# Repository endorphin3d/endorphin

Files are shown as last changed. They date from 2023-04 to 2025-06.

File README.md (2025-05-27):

# Endorphin

This is the repo for both the CAD files and the docs for the Endorphin project. Docs are built and published [here](https://endorphin3d.com/docs).

### Docs

The docs are built using [Jekyll](https://jekyllrb.com/) and [Just the Docs](https://justtheocs.com/).

To serve the docs locally, run:

```sh
bundle exec jekyll serve
```

This will start a local server at `http://localhost:4000`.

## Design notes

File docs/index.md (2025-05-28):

---
layout: default
title: Introduction
nav_order: 1
permalink: docs
has_toc: false
---

{% capture preface %}
In the last few years 3D printers have become blisteringly fast, pushing the limits of both heating and cooling while leaving those of us with printers like the Ender 5 feeling a bit left out of the fun. That ends now. Your Ender 5 is capable of being every bit as fast as a Voron without the hefty price tag. There have been [other](https://zerog.one) CoreXY [projects](https://www.printables.com/model/169131-ender-5-core-xy-with-linear-rails-mk3) to do a full conversion on the Ender 5, but often the price of parts or the complexity of the build makes it hard to justify over just buying something pre-built like a Bambulab P1P.

**The Endorphin is different.**

With a first-stage build you can do in an afternoon with parts that total less than $25, you no longer have any excuses *not* to turn Ender 5 into a speed demon.
{% endcapture %}
{% include docs-preface.html
  title="# Introduction"
  image="/assets/images/docs/getting-started/belt-path.png"
  content=preface
%}

{% capture kinematic %}
The Endorphin uses a slightly different belt setup from the original Ender 5, known as a "Markforged kinematic" or Hybrid CoreXY. In this setup the X belt moves like a CoreXY but the Y axis remains in its original Ender 5 cartesian setup.

### Why Though?

The basic idea is this: The less weight being thrown around, the faster the printer's acceleration/deceleration can be. Less weight also means higher top speeds because there will be less energy required to stop and change direction at the end of each move. This is why the CoreXY setup has become the choice of pretty much all high-speed printers such as the BambuLab, Voron, Ratrig, and HevORT.

This project moves the X stepper motor off the gantry and onto the frame, where the Y steppers won't have to lug it around anymore. This is a significant amount of weight we're saving!

Now, if you know anything about CoreXY machines you know that unlike cartesian printers, CoreXY printers don't have an "X stepper" or a "Y stepper" because a movement of one stepper affects both belts. In the Markforged kinematic, this is only partially the case:

- The X stepper can move the printhead along the X axis by simply moving its belt while the Y belt stays stationary
- The Y stepper only has to worry about moving the gantry linearly along the Y axis (cartesian style)
- BUT when the Y stepper moves the gantry, the length of the X belt on either side of the gantry is affected and thus the X stepper must also move to compensate

### Firmware

Luckily this kinematic is supported by both Klipper and the stock Marlin firmware (with a small modification). After you've printed the parts for at least stage 1, just follow the instructions in the [firmware section](/docs/firmware) to use the new kinematic.
{% endcapture %}
{% include docs-step.html
  heading="## Kinematic"
  image="/assets/images/docs/getting-started/kinematic.png"
  content=kinematic
%}

## Q&A

### What about the Ender 5 Plus?

Yes, as of version 1.1 the 5+ is also fully supported. Just make sure you don't leave slack in the X belt because that's a *long* belt path.

---

[Next →](/docs/stages){: .btn .btn-outline .fs-5 }

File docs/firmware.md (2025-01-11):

---
layout: default
title: Firmware
nav_order: 3
permalink: docs/firmware
has_toc: false
---

# Firmware

{: .warning }
Don't make these changes until *AFTER* you've printed out all the parts for at least stage 1! You need a working printer (or a second printer) to get stage 1 off the ground.

- TOC
{:toc}

---

### Klipper

If you've been thinking about making the leap to Klipper, this might be the push you've been needing. Making config changes to a machine running Klipper is roughly 1000% easier than Marlin. All that's required to configure Klipper to use the new kinematic is editing `printer.cfg` and changing `kinematics` under the `[printer]` section:

```yml
[printer]
kinematics: hybrid_corexy
...
```

Then change your endstop settings under `stepper_x` and `stepper_y` so the printer homes in the right direction:

```yml
[stepper_x]
...
position_endstop: 220
position_max: 220
...

[stepper_y]
...
# Note: These may need to be 190 if using the EVA printhead
position_endstop: 200
position_max: 200
...
```

Now save and restart and you're done. Seriously, you're done.

### Marlin (Original Firmware)

The Marlin firmware is a bit trickier. To change the kinematics here you need to recompile and flash the firmware on your board.

Start by following the instructions on the [Marlin site](https://marlinfw.org/docs/basics/install_platformio_vscode.html) until you reach the section on example configurations where you're told to "find the configuration files for your printer." Assuming you've downloaded the Marlin configurations, you'll now need to pick the folder that corresponds to your printer + board version. The surest way to figure which board you have is to open up the case and check. If you have a 4.2.7 or a 4.2.2, it'll be printed right under the Creality logo in the center of the board. If you have a v1 board, there will be no version printed at all.

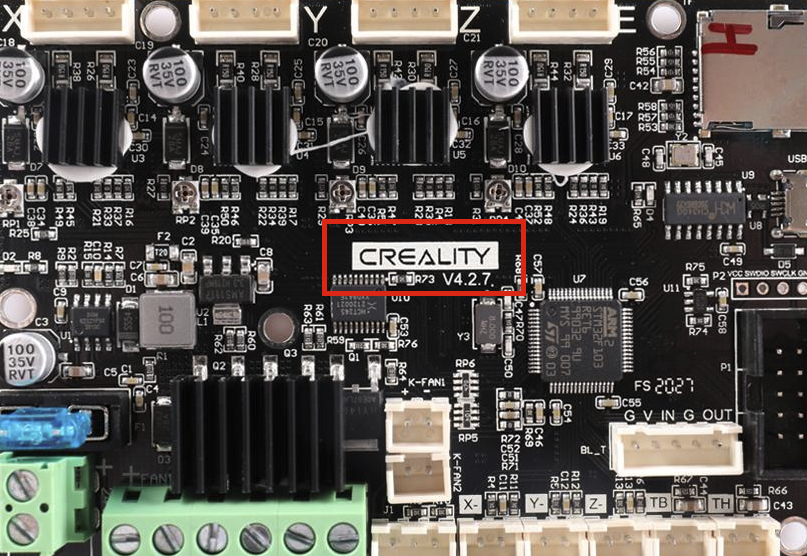
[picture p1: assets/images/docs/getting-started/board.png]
Endorphin stage 1


So for example if you have an Ender 5 Pro with a 4.2.7 board, you'll find the correct configuration in the folder `config/examples/Creality/Ender-5 Pro/CrealityV427`.

Next we need to configure the firmware to use the Markforged kinematic. This only requires editing a single line in the `Configuration.h` file. If you search the file for "MARKFORGED_XY" you should see this line several hundred lines down:

```c
//#define MARKFORGED_XY
```

You'll want to un-comment this line, like so:

```c
#define MARKFORGED_XY
```

Then just below it you'll see:

```c
#if ANY(MARKFORGED_XY, MARKFORGED_YX)
  //#define MARKFORGED_INVERSE  // Enable for an inverted Markforged kinematics belt path
#endif
```

Uncomment that middle line, so it looks like this:

```c
#if ANY(MARKFORGED_XY, MARKFORGED_YX)
  #define MARKFORGED_INVERSE  // Enable for an inverted Markforged kinematics belt path
#endif
```

Now you can continue following the Marlin guide on compiling the new firmware. Once you've compiled, you can put the new firmware file (usually `firmware.bin`) at the root of your microSD card. Just to be 100% certain the printer will recognize the new firmware, rename the file to `firmware-endorphin.bin`. Then with your printer powered off, insert the SD card and power the printer on. Wait a few minutes to ensure the install finishes, then power the printer down and remove the card. Delete `firmware-endorphin.bin` and you're done!

---

[← Back](/docs/stages/stage-3){: .btn .btn-outline .mr-4 .fs-5 }

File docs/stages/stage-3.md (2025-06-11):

---
layout: default
title: Stage 3
nav_order: 3
parent: Stages
permalink: docs/stages/stage-3
---

{% capture preface %}
> The purpose of this stage is to add a linear rail on the X axis. We'll basically be trading the weight from the original steel printhead carriage and its wheels for an MGN9 rail of similar weight (on the plus side, in the Hybrid CoreXY configuration the weight will now be shared between the two stepper motors). Thus, the benefits of this stage aren't as much weight removal as the ability to use a modern printhead such as the Ratrig EVA or the Vz Printhead, plus complete liberation from those frustrating v-slot wheels.
{: .fs-5 .fw-300 .text-grey-dk-100 .text-justify }
{% endcapture %}
{% include docs-preface.html
  title="# Stage 3: Linear X Rail"
  image="/assets/images/docs/stages/stage-3/stage-3-render-lg.png"
  content=preface
%}

---

## Bill Of Materials

#### Linear Rails

| Size | Length | Quantity | Link |
| :--- | :----- | :--- | :--- |
| MGN9H Rail+Block | 350mm  | 1 | [Amazon](https://www.amazon.com/gp/product/B09XQ53J42), [Fabreeko](https://www.fabreeko.com/collections/honeybadger/products/honeybadger-mgn9h-black-steel-rails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) |

#### Bolts

| Part | Type | Quantity | Link |
| :--- | :--- | :--- | :--- |
| M3x8 socket head | ISO 4762, DIN 912 | 8 | [Amazon](https://www.amazon.com/gp/product/B08R3GJGWT) |

#### T-Nuts

| Size | Quantity | Link |
| :--- | :--- | :--- |
| M3 2020 T-nuts | 8 | [Amazon](https://www.amazon.com/gp/product/B08NZMD2BJ) |

---

## Printing

**STL files for this stage are** [here](https://github.com/endorphin3d/endorphin/tree/main/STLs/stage-3)

{% capture vz %}
**Usable Print Area:** 220 x 200 (20mm reduction on Y axis)

The Vz Printhead is an impressively simple printhead used on the blazing fast VzBot printer. It has all the features you'd expect from a modern printhead including many popular hotends, extruders, and Z probes (BLTouch and SuperPINDA). It also as well as some less-common features like adjustable-height fan ducts and CPAP cooling.

The only drawback with this printhead is that you may not already have the [30mm standoffs](https://speedyfpv.com/products/10pcs-m3x30mm-aluminum-spacer-standoff-silver-anodized?variant=37983057936557) on hand to complete the build (< $10 with shipping).

The official design only required three parts to be modified in order to work on the Endorphin. So start by downloading the official STLs from [here](https://github.com/VzBoT3D/Vz-Printhead-Printed/tree/main/STLs) and you can find the BOM [here](https://github.com/VzBoT3D/Vz-Printhead-Printed/tree/main/BOM). Then before you start printing parts, check the table below and substitute any of the original parts listed below with the Endorphin part:

| Original Part | Endorphin Part |
| :--- | :--- |
| Back plate round standoff.stl | [vz-back_plate.stl](https://raw.githubusercontent.com/endorphin3d/endorphin/main/STLs/stage-3/vz-back_plate.stl) |
| Bottom plate round standoff.stl | [vz-bottom_plate.stl](https://raw.githubusercontent.com/endorphin3d/endorphin/main/STLs/stage-3/vz-bottom_plate.stl) |
| Front round standoff.stl | [vz-front.stl](https://raw.githubusercontent.com/endorphin3d/endorphin/main/STLs/stage-3/vz-front.stl) |

{: .note }
Make sure you print the MGN9**H** version of the carriage top (assuming you bought your rails from the links above) rather than the MGN9**C** version.
{% endcapture %}
{% include docs-step.html
  heading="## Vz Printhead"
  image="/assets/images/docs/stages/stage-3/vz.png"
  content=vz
%}

### Belt Clips

Either of the following belt clips provided with the printhead will work fine so pick whichever one you prefer. The original Vz printhead has been modified so that the posts sit at the right height for the Endorphin belts. Just remember that you only need to print off clips for 2 belt ends rather than the 4 needed in a CoreXY, which means you can choose whether you want to attach the belt ends on the front or rear posts (just don't do one front and one rear). The other side will be unused.
{: .mb-8 }

{% capture belts1 %}
This clip is incredibly simple to print and the gripping mechanism is equally simple: By circling the belt around the standoffs, teeth inward, the belt grips itself by interlacing its own teeth like a zipper. This is probably the best choice in terms of printability and simplicity.
{% endcapture %}
{% include docs-step.html
  heading="#### Belt Clip Style 1"
  image="/assets/images/docs/stages/stage-3/belt-clip-1.png"
  content=belts1
%}

{% capture belts2 %}
This is a two-part clip that has more intricate details to print, so make sure to use a small enough nozzle and/or thin layers. While also a clever design, it does look like the wings on the outer clip housing run the risk of spreading under enough tension and allowing the belt to slip.
{% endcapture %}
{% include docs-step.html
  heading="#### Belt Clip Style 2"
  image="/assets/images/docs/stages/stage-3/belt-clip-2.png"
  content=belts2
%}

{% capture eva %}
**Usable Print Area:** 220 x 190 (30mm reduction on Y axis)

The EVA printhead is the standard Ratrig printhead. It has a large number of official addons including fan ducts, hotends, and extruders as well as [even more](https://www.printables.com/search/models?q=tag:eva3) parts created by the community. The main downside of this printhead is that its size causes about 10mm more lost print space on the Y axis than the Vz.

The official EVA v3 design only required three parts to be modified in order to work on the Endorphin, so you can start by reading up on the official [CoreXY printhead](https://main.eva-3d.page/heat_insert/core/corexy) and downloading most of the parts from this page. Just substitute the following parts for the Endorphin versions in this table:

| Original Part | Endorphin Part |
| :--- | :--- |
| back_core_xy_fi.stl | [eva-back_endorphin.stl](https://raw.githubusercontent.com/endorphin3d/endorphin/main/STLs/stage-3/eva-back_endorphin.stl) |
| core_xy_belt_grabber.stl | [eva-endorphin_belt_grabber.stl](https://raw.githubusercontent.com/endorphin3d/endorphin/main/STLs/stage-3/eva-endorphin_belt_grabber.stl) |
| top_endstop_mgn12c_fi | [eva-eva-mgn9h.stl](https://raw.githubusercontent.com/endorphin3d/endorphin/main/STLs/stage-3/eva-mgn9h.stl) |

You also don't need to print `face_belt_grabber.stl` because the Endorphin doesn't have a belt that attaches to the front of the EVA in the same way that a CoreXY does.

After you've printed the core printhead, you can choose the fan duct, hotend, and extruder that suits you. If you don't see your preferred parts on the official site, make sure to check sites like [printables](https://www.printables.com/search/models?q=tag:eva3) for what you need.

Credit for `eva-mgn9h.stl` goes to [@andbou_260448](https://www.printables.com/model/209376-eva-30-heat-set-mgn-9h-top-endstop)

{% endcapture %}
{% include docs-step.html
  heading="## EVA"
  image="/assets/images/docs/stages/stage-3/eva.png"
  content=eva
%}

{% capture evabelts %}
{% endcapture %}
{% include docs-step.html
  heading=""
  video="/assets/vids/docs/stages/stage-3/assembly-endorphin-belts.mp4"
  content=evabelts
%}

{% capture cableguide %}
Let's clean up the cable pathway for your nice new printhead. This is a simple one to print and only needs one M3 T-nut to secure to the frame.

Now just run your cables from the back of the board enclosure straight up and into your printhead!
{% endcapture %}
{% include docs-step.html
  heading="## Cable Guide"
  image="/assets/images/docs/stages/stage-3/cable-guide.png"
  content=cableguide
%}

---

[← Back](/docs/stages/stage-2){: .btn .btn-outline .mr-4 .fs-5 } [Next →](/docs/firmware){: .btn .btn-outline .fs-5 }

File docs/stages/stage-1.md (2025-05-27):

---
layout: default
title: Stage 1
nav_order: 1
parent: Stages
permalink: docs/stages/stage-1
---

{% capture preface %}
> The goal of this stage is to drop the heaviest single part on the X carriage: **The stepper motor**. This stage alone will remove almost half a pound of moving weight but only takes a few hours to print and assemble.
{: .fs-5 .fw-300 .text-grey-dk-100 .text-justify }
{% endcapture %}
{% include docs-preface.html
  title="# Stage 1: Hybrid CoreXY"
  image="/assets/images/docs/stages/stage-1/stage-1-render-lg.png"
  content=preface
%}

---

## Bill Of Materials

#### Bolts

| Part | Type | Quantity |
| :--- | :--- | :--- |
| M3x12 socket head | ISO 4762, DIN 912 | 4 |
| M3x25 socket head | ISO 4762, DIN 912 | 4 |
| M5X25 hex head | ISO 4017, DIN 933 | 1 |

#### Washers

| Part | Type | Quantity |
| :--- | :--- | :--- |
| M3 | DIN 125 | 6 |

#### Hex Nuts

| Part | Type | Quantity |
| :--- | :--- | :--- |
| M3-0.5 hex nut | DIN 934 | 3 |
| M5-0.8 hex nut | DIN 985, ISO 10511 | 1 |

#### Belt

| Part | Size | Quantity | Link |
| :--- | :--- | :--- | :--- |
| GT2 belt | 6mm wide, 5m long | 1 | [Amazon](https://www.amazon.com/Upgrade-Non-Slip-Version-Printer-Printers/dp/B08R93QQ8Z) |

#### Pulleys

| Part | Size | Quantity | Link |
| :--- | :--- | :--- | :--- |
| GT2 toothless idler | 3mm bore, 20-tooth diameter | 5 | [Amazon](https://www.amazon.com/BZ-3D-Aluminum-Printer-Toothless/dp/B08726CGYJ) |

---

{% capture printing %}
**STL files for this stage are** [here](https://github.com/endorphin3d/endorphin/tree/main/STLs/stage-1)

It should be easy to guess the print orientation for most of these parts. The only difficult one is the oddly-shaped front corner assembly. There's one particularly flat face on the part that has no fillets on the corners; this is the face that was designed to be on the print bed.

You should use **100% infill** for these parts and at least **4 perimeters/walls** (for screw hole durability). Parts printed with 0.2mm layer height look fantastic but 0.24mm is several hours faster.
{: .text-justify }
{% endcapture %}
{% include docs-step.html
  heading="## Printing"
  image="/assets/images/docs/stages/stage-1/plating.png"
  content=printing
%}

{% capture fca %}
1. Remove screws from front-right Y tensioner plate and set them aside for step 3
1. Remove the screw from the tensioner keeping the Y belt captured
1. Attach the front corner piece, reusing the M5 bolt and one of the M4 T-nut screws from the original plate on one side and the other M4 T-nut on the other corner of the aluminum extrusion
{% endcapture %}
{% include docs-step.html
  heading="## Front Corner Assembly"
  video="/assets/vids/docs/stages/stage-1/assembly-front-corner.mp4"
  content=fca
%}

{% capture pulleys %}
Next you'll install the right Y belt tensioner and the X belt's front pulley. If you bought the 5 pack of smooth pulleys linked in the BOM, you can use those both here and as the center pulleys.

1. Hook the X belt onto a 20-tooth, 3mm bore pulley and slide it into place
1. Add a washer to the top and bottom of the pulley
1. Insert an M3x25 screw through the top and secure it onto the underside with a hex nut
1. Insert the M5 hex nut into the hexagon slot on the inside of the Y belt tensioner and an M3 hex nut into the slot on the outer right side
1. Hook the Y belt on another 20-tooth pulley and slide it into the tensioner housing
1. (Optional) Add a washer on both sides of the pulley. This isn't as critical as the other pulleys which are pulled into plastic due to gravity
1. Place the tensioner housing inside the corner assembly and secure it into place with an M3x25 screw which will pass through housing and pulley and thread into the hex nut on the other side. The tensioner housing should now slide forward and back to tension the belt.
1. Push the M5 bolt through the tensioner knob and thread it into the tensioner housing. Twist the knob until the right Y belt is as tight as the left.
{% endcapture %}
{% include docs-step.html
  heading="## Front Pulleys"
  video="/assets/vids/docs/stages/stage-1/assembly-driven-pulleys.mp4"
  content=pulleys
%}

{% capture x-stepper %}
1. Remove the screws on the back-right Y-axis pulley bracket and set aside
1. Install the new stepper mount by on top of the old bracket, putting the screws back in the same places they were
1. Remove the X stepper from the X gantry by removing the 4 screws on the top
1. Move the stepper to its new mount and secure it with four M3x12 screws
{% endcapture %}
{% include docs-step.html
  heading="## Move The X Stepper"
  video="/assets/vids/docs/stages/stage-1/assembly-driving-mount.mp4"
  content=x-stepper
%}

{% capture center-idlers %}
These two center idlers are the reason we're using ones with a 3mm bore throughout the project rather than the more common 5mm bore. Because we're making use of two of the stepper mounting holes on the original X stepper plate to hold the axles for the idlers. These holes are only large enough to use M3 screws as axles, hence the 3mm bore pulleys.

1. Remove the old X belt if you haven't already
1. Place the bottom center idler block on top of the carriage (the bottom plate is the one without the hexagon holes)
1. Sandwich two pulleys between washers and set them on top of the idler block
1. Insert two M3 hex nuts into the top idler block and place on top of the pulleys
1. Drive two M3x25 screws from the underside, passing through the holes original steel plate and then through our stack of new parts, finally threading into the hex nuts in the top center idler block
{% endcapture %}
{% include docs-step.html
  heading="## Center Idlers"
  video="/assets/vids/docs/stages/stage-1/assembly-center-idlers.mp4"
  content=center-idlers
%}

### A Note On Washers

These little M3 washers can be tricky to install, and you may be tempted to skip them altogether. A good rule of thumb is anywhere that gravity is at play on a pulley, you'll need a washer so it doesn't rub. In short: Washers are going to be *highly* recommended on the X axis pulleys, but not so critical on the Y tensioners.

## Optional Steps

### Swap Motors
{: .d-inline-block }

Highly Recommended
{: .label .label-red .my-0 }

In the original Ender 5, the X stepper only needed to be strong enough to move the printhead. Now it will be sharing the weight of the entire carriage with the Y stepper (which you'll notice is a bigger motor). This is why it's highly recommended to swap the extruder stepper and the X stepper. This will allow you to reach higher speeds without skipping.

### Tune Stepper Current
{: .d-inline-block }

If you find that your X stepper motor is getting hot during long prints, you can turn your stepper current down a bit. Just follow [this guide](https://all3dp.com/2/vref-calculator-tmc2209-tmc2208-a4988) which should only take a few minutes to complete.

### Stealthchop and Torque
{: .d-inline-block }

Klipper Only
{: .label .label-blue .my-0 }

Stealthchop is a feature in many modern boards which quiets the stepper motor at the expense of slight inaccuracies and reduced torque. For maximum speeds, you would want to **disable** Stealthchop. Unfortunately the "silent" boards that come in the Ender 5 require some soldering to disable Stealthchop (look up "Creality 4.2.2 and 4.2.7 UART mod").

That said, if you have a more modern board, you can disable Stealthchop for maximum torque while increasing your micro-steps to achive a very similar level of quiet from your steppers. Here's what you would add to your printer.cfg (change "tmc2209" to your model's stepper driver):

```yaml
[stepper_x]
...
microsteps: 128
rotation_distance: 40

[tmc2209 stepper_x]
...
run_current: 0.620
interpolate: False

[stepper_y]
...
microsteps: 128
rotation_distance: 40

[tmc2209 stepper_y]
...
run_current: 0.650
interpolate: False
```

## Troubleshooting

### Height adjustments

Once you've installed and tightened your hybrid X belt you might notice that it's not running perfectly parallel all the way along its path, or you might find that it's slightly too high or low and it's rubbing against the X rail after it passes through the center idlers. If this happens, there's a number of adjustments you can make, depending on what the issue is.

1. Raise/lower the pulley on the X motor (many but not all Ender 5 models have an adjustable grub screw on the pulley)
1. Raise the center idlers with another washer
1. Raise the front corner idler with another washer

### Quacking Noise

Sometimes during printing, mainly on faster travel moves, you might hear a sound that's reminiscent of an oversized goose honking. While it may seem like a mechanical issue (something rubbing, needing oil, etc.) it actually goes away completely when disabling StealthChop (see the StealthChop section above).

---

[← Back](/docs/stages){: .btn .btn-outline .mr-4 .fs-5 } [Next →](/docs/stages/stage-2){: .btn .btn-outline .fs-5 }

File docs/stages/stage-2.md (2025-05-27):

---
layout: default
title: Stage 2
nav_order: 2
parent: Stages
permalink: docs/stages/stage-2
---

{% capture preface %}
> The goal of this stage is to drop the next heaviest parts on the X carriage: The V-slot wheels and steel mounts. This will yield us another **270g** of moving weight reduction--that's another half pound!
{: .fs-5 .fw-300 .text-grey-dk-100 .text-justify }
{% endcapture %}
{% include docs-preface.html
  title="# Stage 2: Linear Y Rails"
  image="/assets/images/docs/stages/stage-2/stage-2-render-lg.png"
  content=preface
%}

---

## Bill Of Materials

#### Linear Rails

| Size | Length | Quantity | Link |
| :--- | :----- | :--- | :--- |
| MGN12H Rail+Block | 300mm  | 2 | [Amazon](https://www.amazon.com/gp/product/B09QPCTYDM), [Fabreeko](https://www.fabreeko.com/collections/honeybadger/products/honeybadger-mgn12h-black-steel-rails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) |

#### Bolts

| Part | Type | Quantity | Link |
| :--- | :--- | :--- | :--- |
| M3x8 socket head | ISO 4762, DIN 912 | 20 | [Amazon](https://www.amazon.com/gp/product/B08R3GJGWT) |

#### T-Nuts

| Size | Quantity | Link |
| :--- | :--- | :--- |
| M3 2020 T-nuts | 12 | [Amazon](https://www.amazon.com/gp/product/B08NZMD2BJ) |

---

{% capture printing %}
**STL files for this stage are** [here](https://github.com/endorphin3d/endorphin/tree/main/STLs/stage-2)

The right Y rail mount is best printed on its side, but you'll need to make sure your bridge and support settings are dialed in pretty well to prevent sagging and any support interface being left behind (the tolerances for the aluminum extrusion are pretty tight on purpose).

The left mount can be printed in the same orientation *or* on its back. While this makes it easier to print and get correct tolerances against the aluminum extrusion, the strength at the belt attachment points is theoretically lower than being printed on the side.

{: .text-justify }
{% endcapture %}
{% include docs-step.html
  heading="## Printing"
  image="/assets/images/docs/stages/stage-2/plating.png"
  content=printing
%}

{: .note }
A great help in mounting the rails is a [rail alignment tool](https://www.thingiverse.com/thing:3533580). There are several other similar alignment tools on Thingiverse and Printables if you don't like this one. You'll want to print this tool before beginning the next step.

{% capture left %}
1. Loosen the X and Y belts then slide the Y belts out of the wheel plates. You won't be able to reuse these belts so you can toss them.
1. Remove the v-slot wheel screws and wheels on the left wheel plate
1. Remove the two M5 screws on the underside of the plate which attach it to the X gantry and **save these for later**
1. The plate can now be removed from the gantry
1. Using M3x8 screws and T-nuts, secure the MGN12 rail to the **outside** of the frame (this is where the alignment tool comes in handy)
1. Attach your new left linear mount (the smaller of the two) to the linear bearing block (the slidey thing) using M3x8 screws
1. Press the X gantry into the 20mm cutout in the mount then use one of the M5 screws from step 3 to secure mount to the X gantry from the underside
1. Fish one end of the Y belt through from the top of the new rail mount, then out the bottom and back in the direction it orginated
1. Secure the belt against its own teeth using a zip tie or [belt clip](https://raw.githubusercontent.com/endorphin3d/endorphin/main/STLs/stage-3/belt_clip-touthed.stl) designed by the [VzBot team](https://github.com/VzBoT3D/Vz-Printhead-Printed).

{% endcapture %}
{% include docs-step.html
  heading="## Left Rail"
  video="/assets/vids/docs/stages/stage-2/assembly-left-linear-y.mp4"
  content=left
%}

{% capture right %}
1. Remove the v-slot wheel screws and wheels on the right wheel plate
1. Remove the two screws on the underside of the plate which attach it to the X gantry and save one of these screws for later
1. The plate can now be removed from the gantry
1. Remove the center idlers and the sandwich blocks. You won't be needing the bottom block but the top one will be reused.
1. Using M3x8 screws and T-nuts, attach the MGN12 rail to the **outside** of the frame (again, using the alignment tool)
1. Attach your new right linear mount to the linear bearing block using M3x8 screws
1. Press the X gantry into the 20mm cutout in the mount then use one of the M5 screws from step 2 to secure mount to the X gantry from the underside
1. Reattach the center idlers as the were before, minus the bottom block. **Don't forget the M3 washers on both sides of the pulleys!**
1. Fish one end of the Y belt through from the top of the new rail mount, then out the bottom and back in the direction it orginated
1. Secure the belt against its own teeth using a zip tie or belt clip

{% endcapture %}
{% include docs-step.html
  heading="## Right Rail"
  video="/assets/vids/docs/stages/stage-2/assembly-right-linear-y.mp4"
  content=right
%}

## Optional Upgrades

{% capture ytensioner %}
While your Y belts are off why not give yourself a nice modern tensioner on the left side like you have on the right?

The design is exactly the same as the right tensioner, so you just need to print a second [knob](https://raw.githubusercontent.com/endorphin3d/endorphin/main/STLs/stage-1/tensioner-knob.stl) and [slider](https://raw.githubusercontent.com/endorphin3d/endorphin/main/STLs/stage-1/tensioner-slider.stl) from stage 1 plus the [tensioner housing](https://raw.githubusercontent.com/endorphin3d/endorphin/main/STLs/stage-2/y-tensioner-housing.stl). The hardware is also exactly the same as the right one (one M5x25 bolt and nut, one M3x25 screw and nut, and one 3mm pulley).

To secure it to the frame, just use one of the M4 T-nuts from the old tensioner. Assembly is the same as the right side.

{% endcapture %}
{% include docs-step.html
  heading="### Left Y Tensioner"
  image="/assets/images/docs/stages/stage-2/left-y-tensioner.png"
  content=ytensioner
%}

{% capture xtensioner %}
In addition to making belt tightening much easier and precise, this will also drop a bit more weight from the X gantry.

Assembly here is pretty straightforward. Remember when you saved the M5 screws from the wheel plates? Well, because those M5 threads were cut all the way through the extrusion, we can reuse that hole to secure our X tensioner from the top! It will be held from wobbling on side-to-side by the lower peg that slots right into your left Y rail block.

The rest of the parts (the slider, knob, and hardware) are the same as the other tensioners. You'll just need to print the main housing [here](https://raw.githubusercontent.com/endorphin3d/endorphin/main/STLs/stage-2/x-tensioner-housing.stl) then assemble it like the others.

{% endcapture %}
{% include docs-step.html
  heading="### X Tensioner"
  video="/assets/vids/docs/stages/stage-2/x-tensioner.mp4"
  content=xtensioner
%}

{% capture xtensionerplating %}
There's a flatter side near the back to make printing easier. The auto-orient feature of many slicers should pick the right side. If your overhang/cooling settings are dialed in you might not even need support!

{% endcapture %}
{% include docs-step.html
  heading="#### Plating"
  image="/assets/images/docs/stages/stage-2/x-tensioner-plating.png"
  content=xtensionerplating
%}
---

[← Back](/docs/stages/stage-1){: .btn .btn-outline .mr-4 .fs-5 } [Next →](/docs/stages/stage-3){: .btn .btn-outline .fs-5 }

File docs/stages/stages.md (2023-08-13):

---
layout: default
title: Stages
nav_order: 2
has_children: true
permalink: docs/stages
has_toc: false
---

# Stages

{: .fs-5 .fw-300 }
Endorphin was designed to be progressively upgraded--so you can get started with minimal cost and time, then upgrade further if you wish. Each stage will drop more moving weight, but will also require more materials and printed parts.

| Stage | Moving Weight Reduction | Cost |
| :--- | :--- | :--- |
| 1 | 215g | $21 |
| 2 | 270g | $38 |
| 3 | 90g[^1] | $16 |
| **Total** | **575g** | **$75** |

> Note: Weight reduction and cost of each stage are listed relative to the stage before it (rather than cumulatively). Grand totals of all the stages are added up in the final row of this table:
{: .fs-4 .fw-300 }

---

[← Back](/docs/getting-started){: .btn .btn-outline .mr-4 .fs-5 } [Next →](/docs/stages/stage-1){: .btn .btn-outline .fs-5 }

[^1]: Because stage 3 adds a linear rail to the X axis, the weight of the new rail does negate the weight saved by dropping the v-slot printhead carriage, but in the Hybrid CoreXY configuration the weight will now be shared between the two stepper motors.

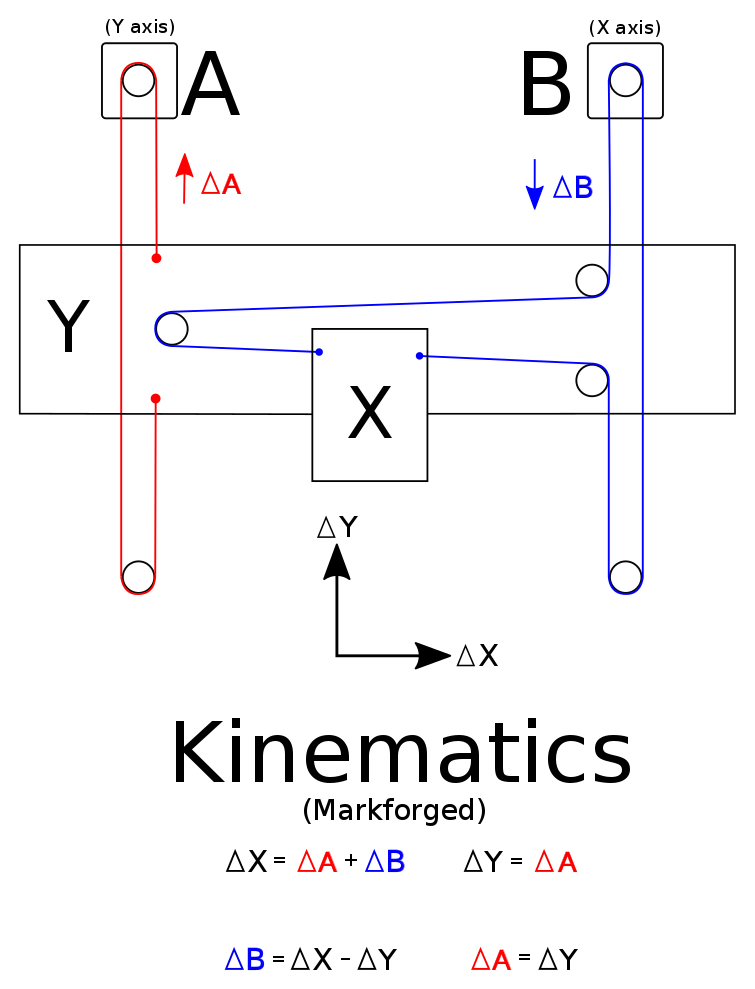
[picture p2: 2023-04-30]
assets/images/docs/getting-started/kinematic.png

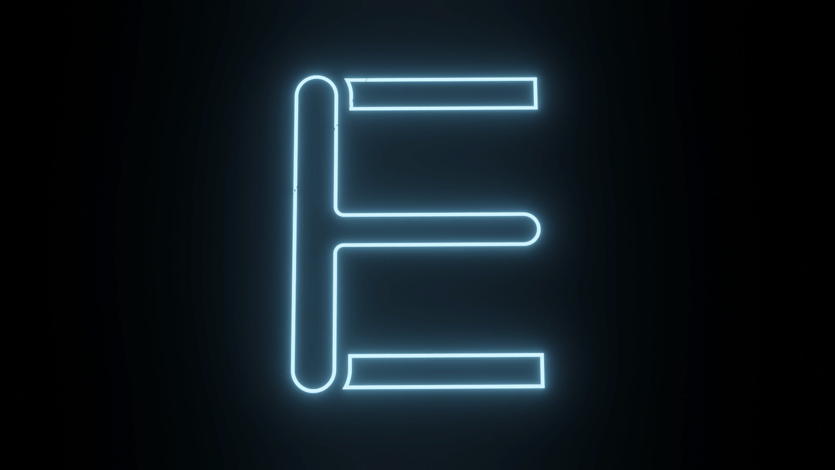
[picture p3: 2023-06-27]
assets/images/poster.png

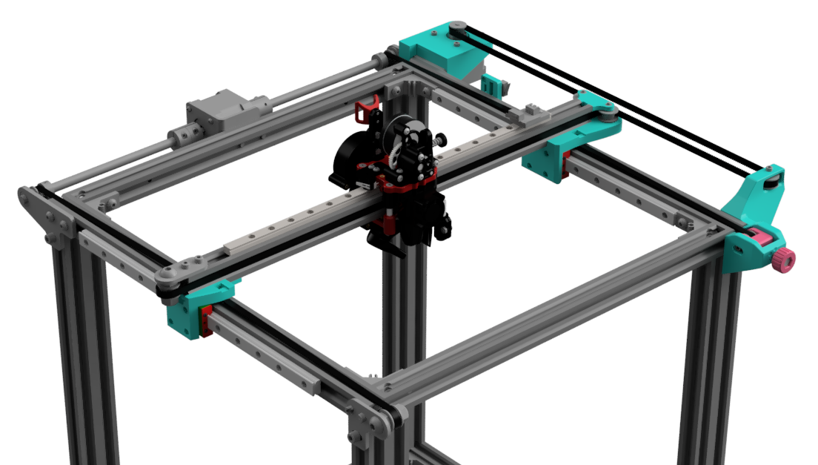
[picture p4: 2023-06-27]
assets/images/poster2.png

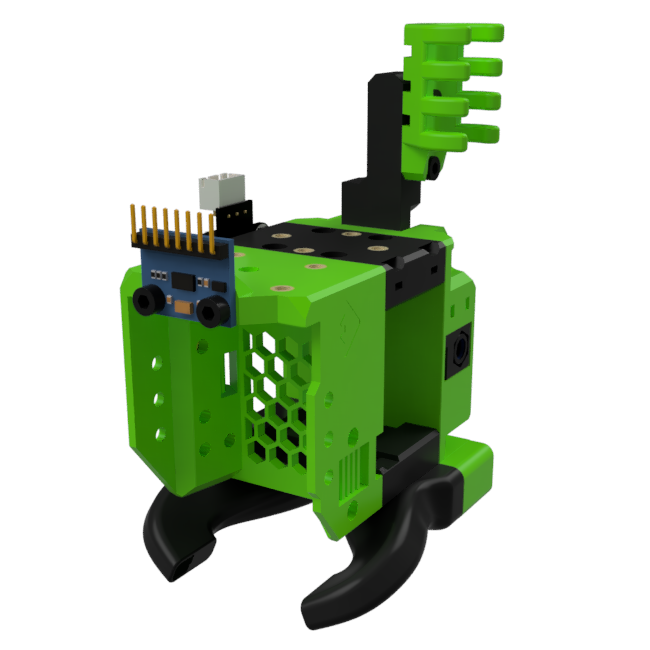
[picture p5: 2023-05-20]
assets/images/docs/stages/stage-3/eva.png

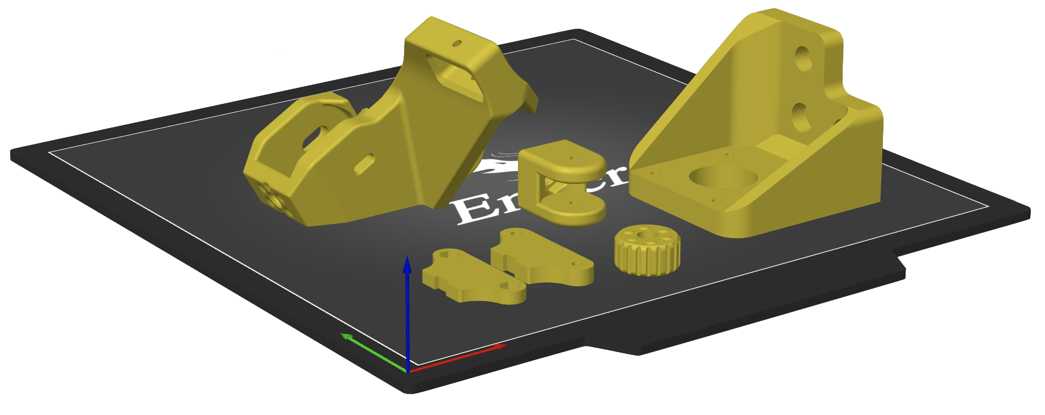
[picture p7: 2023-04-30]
assets/images/docs/stages/stage-1/plating.png

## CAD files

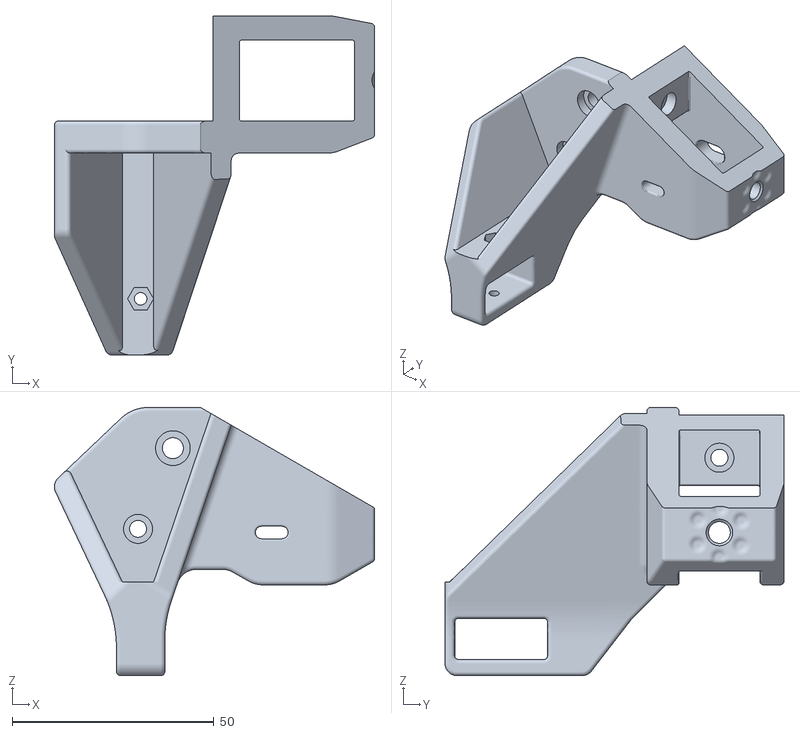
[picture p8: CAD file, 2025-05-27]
STLs/stage-1/front-corner-assembly.stl
79.4 x 84.0 x 66.5

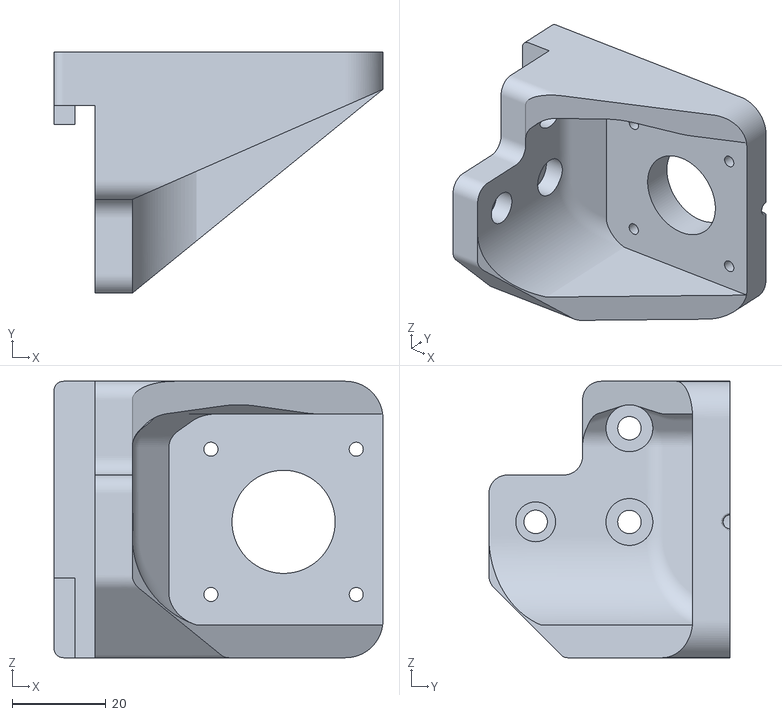
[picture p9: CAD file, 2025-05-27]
STLs/stage-1/driving-x-mount.stl
70.2 x 51.5 x 59.0

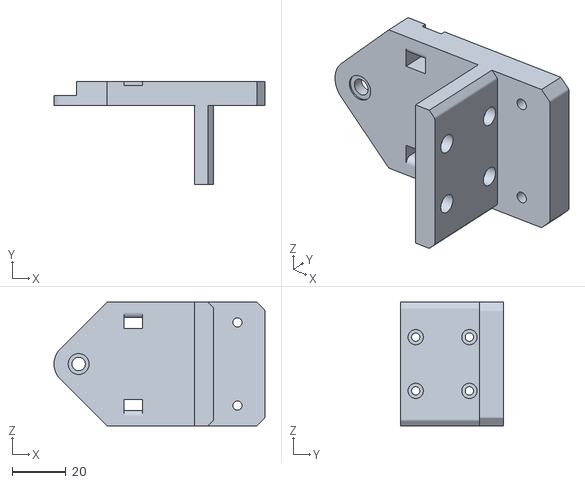
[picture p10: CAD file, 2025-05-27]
STLs/stage-2/right-linear-y.stl
78.6 x 38.3 x 46.0

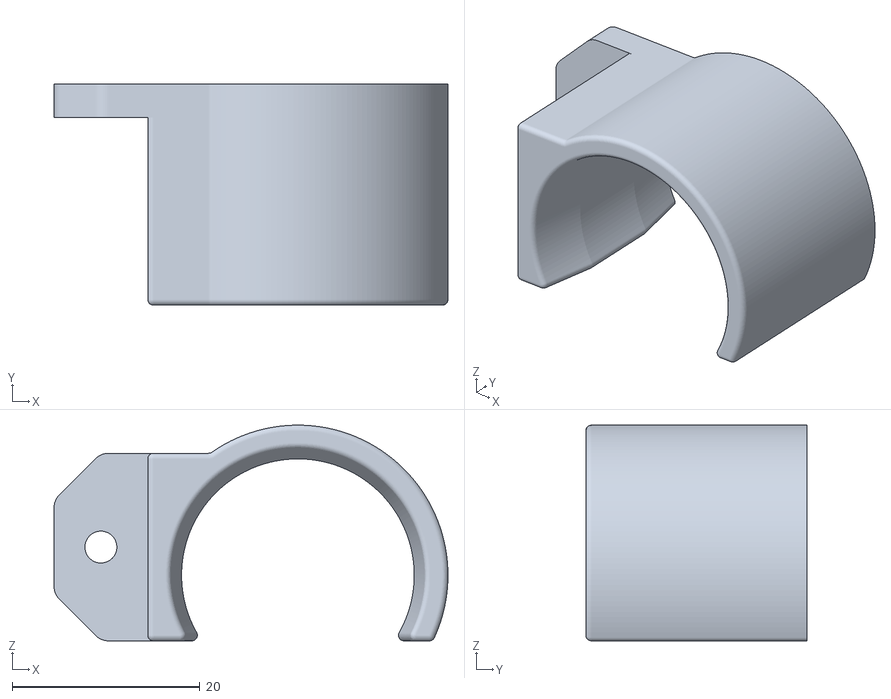
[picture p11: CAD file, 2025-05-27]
STLs/stage-3/cable-guide.stl
42.0 x 23.6 x 23.0

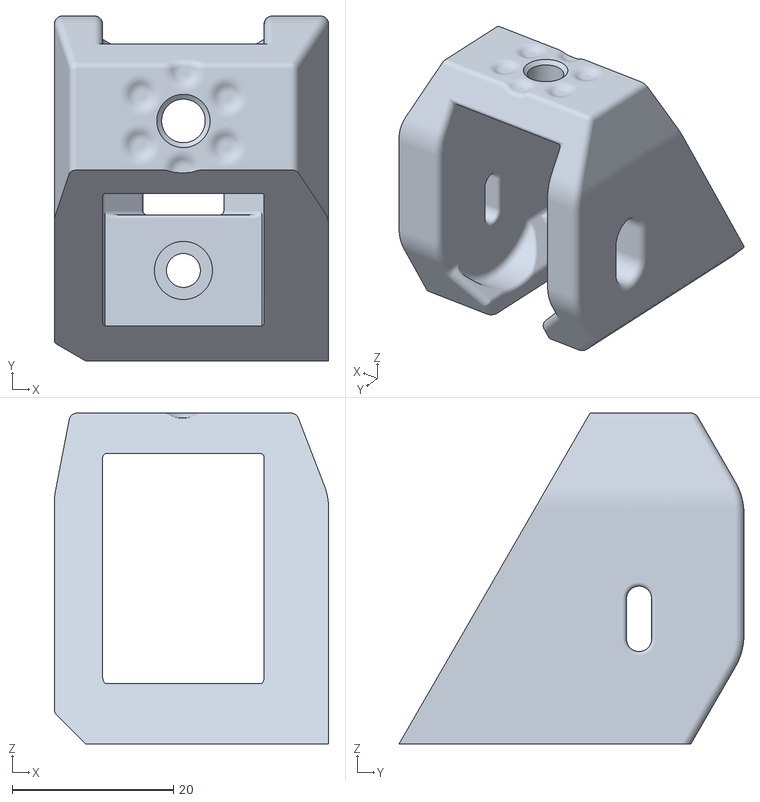
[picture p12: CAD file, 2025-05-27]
STLs/stage-2/y-tensioner-housing.stl
34.0 x 42.7 x 41.0

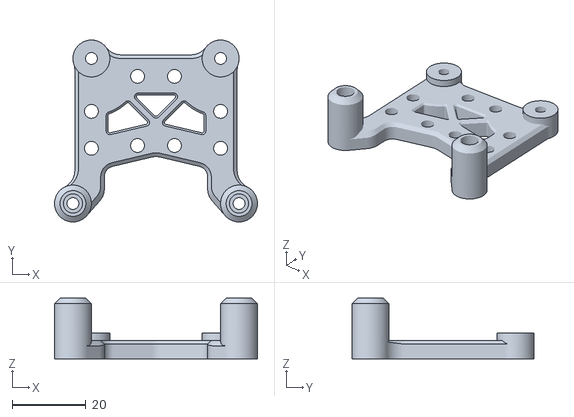
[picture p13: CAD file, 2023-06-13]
STLs/stage-3/vz-bottom_plate.stl
55.0 x 49.3 x 16.5

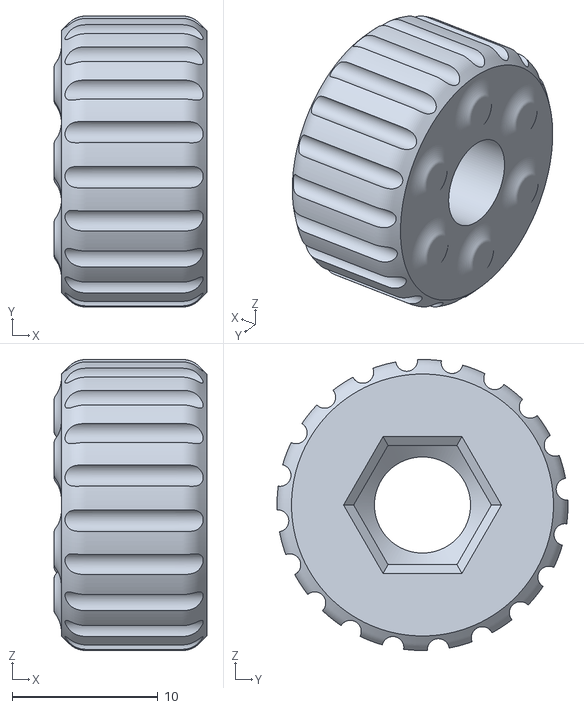
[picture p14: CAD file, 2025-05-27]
STLs/stage-1/tensioner-knob.stl
10.5 x 20.0 x 20.0

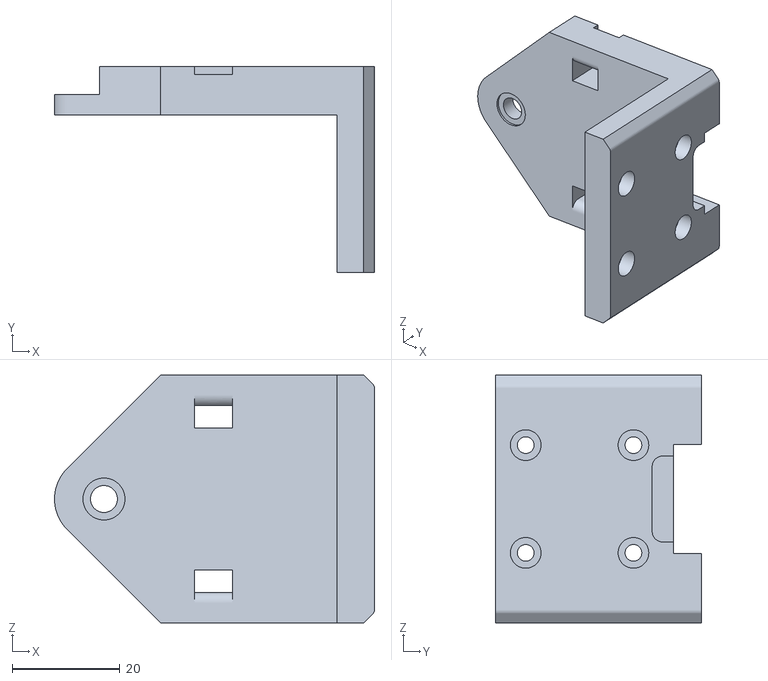
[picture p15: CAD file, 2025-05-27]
STLs/stage-2/left-linear-y.stl
59.4 x 38.3 x 46.0

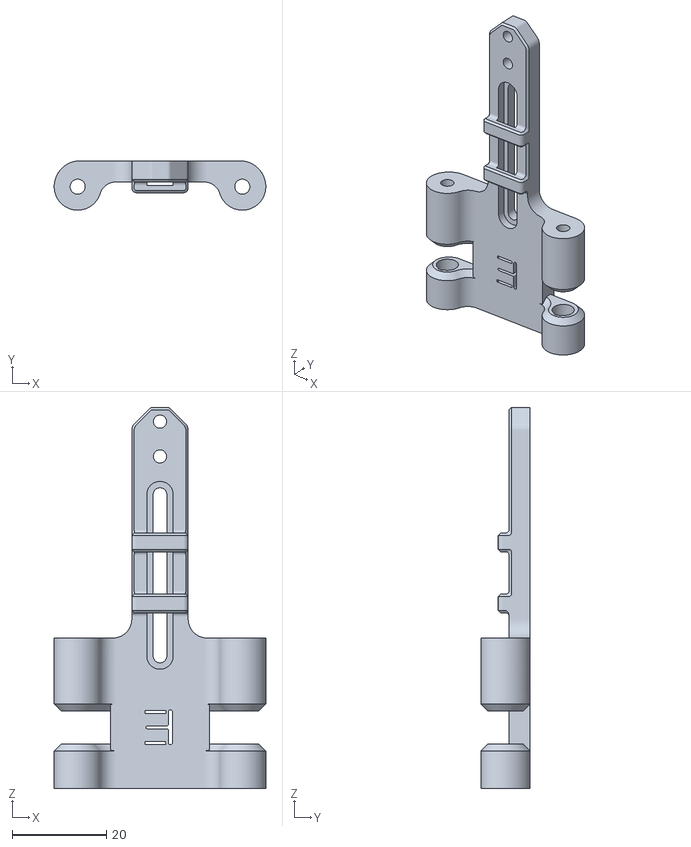
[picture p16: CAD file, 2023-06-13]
STLs/stage-3/vz-back_plate.stl
45.0 x 10.5 x 81.0

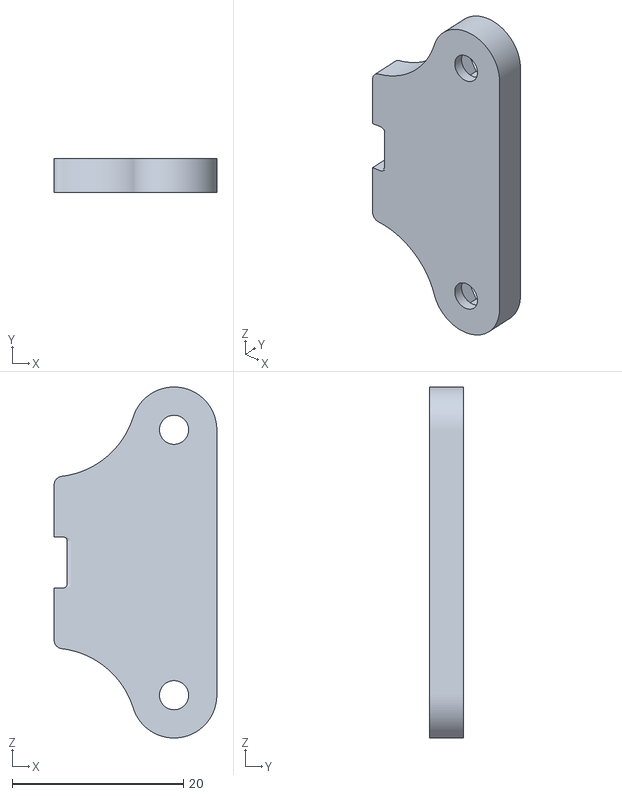
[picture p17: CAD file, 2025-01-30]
STLs/stage-1/center-idler-top.stl
19.0 x 4.00 x 41.0

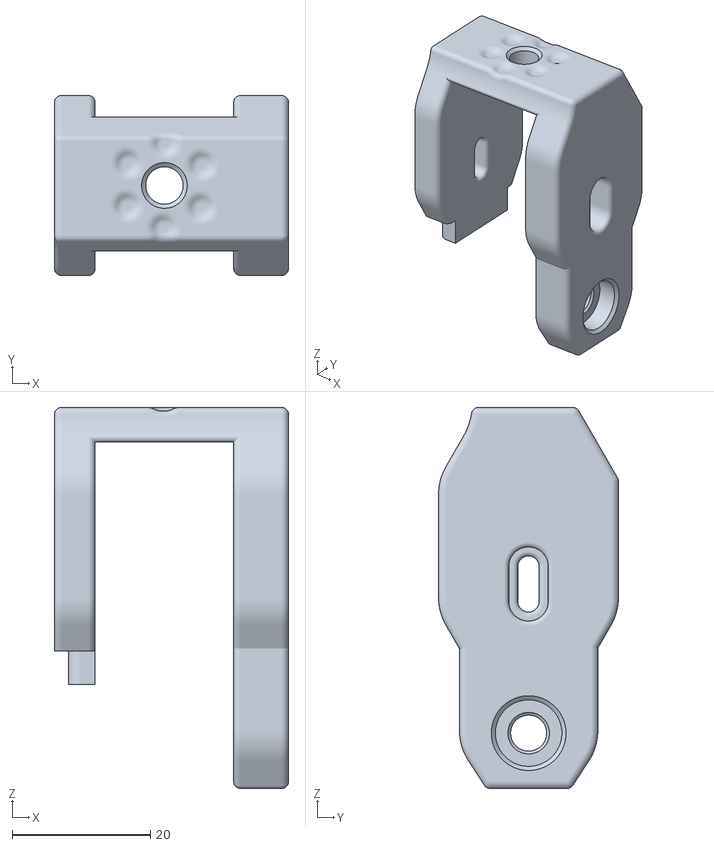
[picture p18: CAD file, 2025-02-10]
STLs/stage-2/x-tensioner-housing.stl
33.8 x 26.0 x 55.0

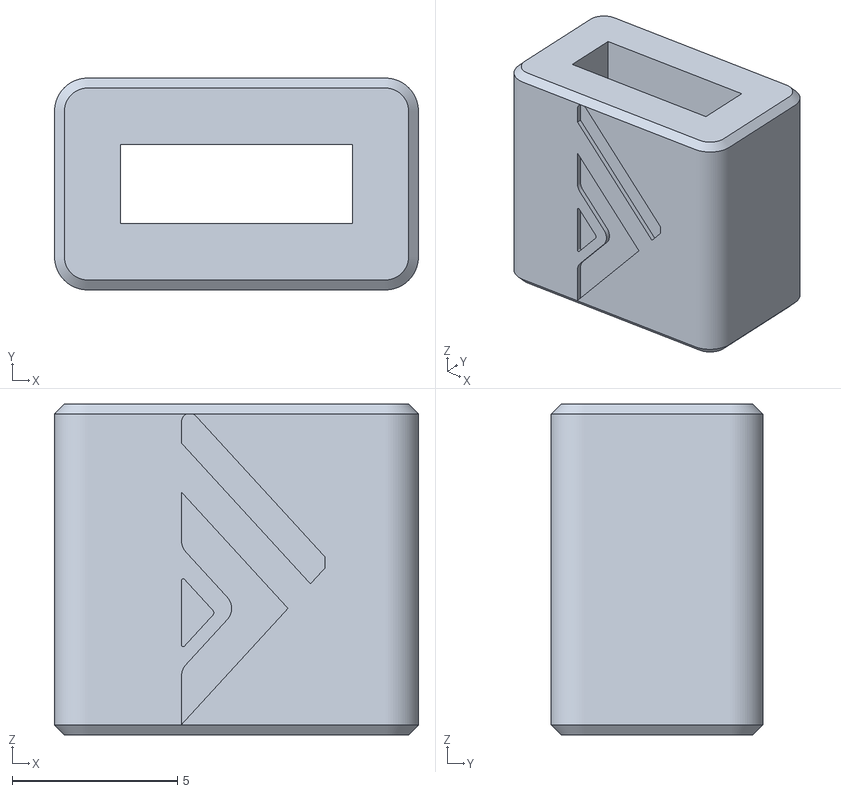
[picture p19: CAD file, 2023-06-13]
STLs/stage-3/belt_clip-touthed.stl
11.0 x 6.40 x 10.0

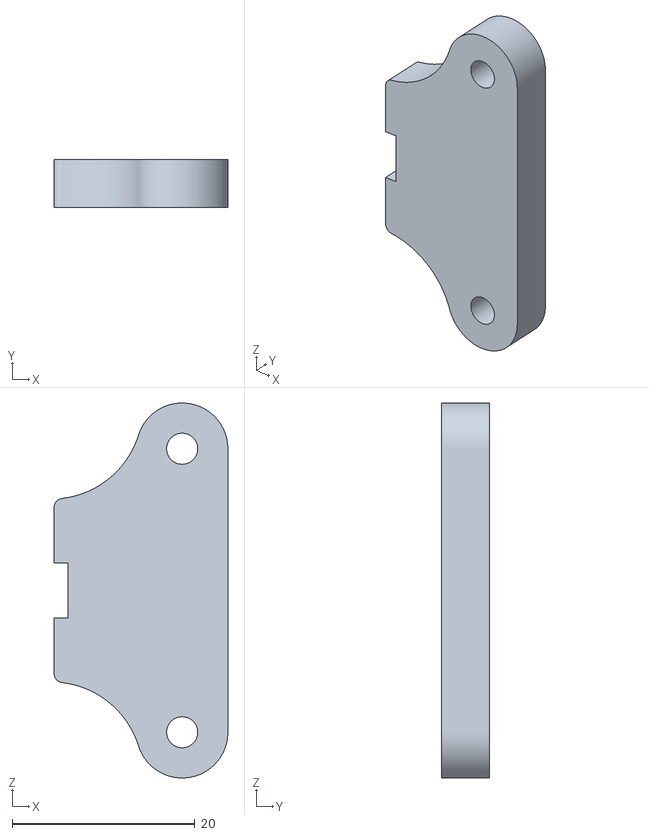
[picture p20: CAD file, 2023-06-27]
STLs/stage-1/center-idler-bottom.stl
19.0 x 5.20 x 41.0

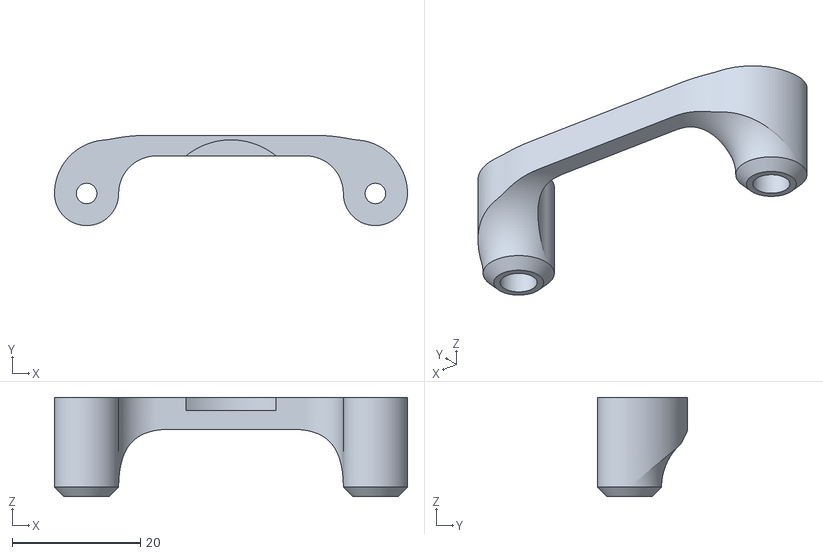
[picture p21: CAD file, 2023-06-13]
STLs/stage-3/vz-front.stl
55.0 x 14.1 x 15.5

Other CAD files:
STLs/stage-1/tensioner-slider.stl
STLs/stage-2/y-endstop.stl
STLs/stage-3/eva-mgn9h.stl
STLs/stage-3/eva-back_endorphin.stl
STLs/stage-3/eva-endorphin_belt_grabber.stl

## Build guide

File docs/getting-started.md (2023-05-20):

---
layout: default
title: Getting Started
nav_order: 1
permalink: docs/getting-started
has_toc: false
---

{% capture preface %}
The Endorphin uses a slightly different belt setup from the original Ender 5, known as a "Markforged kinematic" or Hybrid CoreXY. In this setup the X belt moves like a CoreXY but the Y axis remains in its original Ender 5 cartesian setup--one of the main reasons why the Endorphin is is so much faster to build than a CoreXY conversion.
{% endcapture %}
{% include docs-preface.html
  title="# Getting Started"
  image="/assets/images/docs/getting-started/belt-path.png"
  content=preface
%}

{% capture kinematic %}
Now, if you know anything about CoreXY machines you know that unlike cartesian printers, CoreXY printers don't have an "X stepper" or a "Y stepper" because a movement of one stepper affects both belts. In the Markforged kinematic, this is only partially the case:

- The X stepper can move the printhead along the X axis by simply moving its belt while the Y belt stays stationary
- The Y stepper only has to worry about moving the gantry linearly along the Y axis (cartesian style)
- BUT when the Y stepper moves the gantry, the length of the X belt on either side of the gantry is affected and thus the X stepper must also move to compensate

Luckily this kinematic is supported by both Klipper and the stock Marlin firmware (with a small modification).
{% endcapture %}
{% include docs-step.html
  heading="#### Motion Diagram"
  image="/assets/images/docs/getting-started/kinematic.png"
  content=kinematic
%}

## Software

{: .warning }
Don't make these configuration changes until *AFTER* you've printed out all the parts for at least stage 1! You need a working printer (or a second printer) to get stage 1 off the ground.

### Klipper

If you've been thinking about making the leap to Klipper, this might be the push you've been needing. Making config changes to a machine running Klipper is roughly 1000% easier than Marlin. All that's required to configure Klipper to use the new kinematic is editing `printer.cfg` and changing `kinematics` under the `[printer]` section:

```yml
[printer]
kinematics: hybrid_corexy
...
```

Now save and restart and you're done. Seriously, you're done. You can skip on to the [next page](/docs/stages) now.

### Marlin (Original Firmware)

The Marlin firmware is a bit trickier. To change the kinematics here you need to recompile and flash the firmware on your board.

Start by following the instructions on the [Marlin site](https://marlinfw.org/docs/basics/install_platformio_vscode.html) until you reach the section on example configurations where you're told to "find the configuration files for your printer." Assuming you've downloaded the Marlin configurations, you'll now need to pick the folder that corresponds to your printer + board version. The surest way to figure which board you have is to open up the case and check. If you have a 4.2.7 or a 4.2.2, it'll be printed right under the Creality logo in the center of the board. If you have a v1 board, there will be no version printed at all.

Endorphin stage 1

So for example if you have an Ender 5 Pro with a 4.2.7 board, you'll find the correct configuration in the folder `config/examples/Creality/Ender-5 Pro/CrealityV427`.

Next we need to configure the firmware to use the Markforged kinematic. This only requires editing a single line in the `Configuration.h` file. If you search the file for "MARKFORGED_XY" you should see this line several hundred lines down:

```c
//#define MARKFORGED_XY
```

You'll want to un-comment this line, like so:

```c
#define MARKFORGED_XY
```

Now you can continue following the Marlin guide on compiling the new firmware. Once you've compiled, you can put the new firmware file (usually `firmware.bin`) at the root of your microSD card. Just to be 100% certain the printer will recognize the new firmware, rename the file to `firmware-endorphin.bin`. Then with your printer powered off, insert the SD card and power the printer on. Wait a few minutes to ensure the install finishes, then power the printer down and remove the card. Delete `firmware-endorphin.bin` and you're done!

---

[Next →](/docs/stages){: .btn .btn-outline .fs-5 }

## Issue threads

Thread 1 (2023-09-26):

Difficulty configuring marlin

powermandan, 2023-09-26:
Hi, I have implemented stage one of endorphin. I having problems with the firmware. I'm am no stranger to building marlin firmware.

When you build firmware like this:
#define MARKFORGED_XY
#define INVERT_X_DIR false
#define INVERT_Y_DIR false

X moves in correct direction when operated on its own. When you move Y it moves in correct direction. But the X moves as well. The X stepper is trying to compensate. But it turning the wrong way.

When you set it up like this
#define MARKFORGED_XY
#define INVERT_X_DIR True
#define INVERT_Y_DIR false

The X moves in the opposite direction to expected. When you move Y it goes in correct direction and the X is adequately compensated and remains still on gantry. What this is means is the printer is now effectively mirrored. When I try to home it does to wrong end of gantry.

Any Ideas? As a last resort I am considering reprinting and moving X stepper to other side of printer. My suspicion is that it will work then. Although the maths make my head spin

endorphin3d, 2023-09-26:
Yes, it seems that a few users have experienced this same thing. It seems to be board-dependent as I've never had this issue. One Reddit user (u/Xyzjin) had this to say:

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

So I would give those home direction settings a try and report back. If you find that works for you as well, I will update the docs to include this.

powermandan, 2023-09-27:
I reprinted the parts today and mirrored them to the other side.

In Marlin Inverted X

And I'm happy to report that home has moved back to the normal position and parts are not printed in mirror.

Thanks for taking the time to create this mod

SirNukalot, 2023-09-30:
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

I've also think the reason behind you have to invert the X or Y is because the scematic of the Markforged CoreXY is not matching the Ender5 placement of the stepper-motors. So in the Markforged scematic the Y-stepper axis is facing upright while on the Ender5 it is tilted to the left, so the direction of movement is switched. There was also a commenter who switched the belt attachment points of the x-gantry from front to back and worked around with this solution.

endorphin3d, 2023-09-30:
I appreciate you sharing your findings here. I updated the docs for Klipper to change the endstop settings for correct homing:

```
[stepper_x]
...
position_endstop: 220
position_max: 220
...

[stepper_y]
...
position_endstop: 200
position_max: 200
...
```

Marlin seems to be similar but I haven't quite gathered the exact right settings from people, as I'm on Klipper myself.

powermandan, 2023-09-30:
I am waiting for a klipper Pad to turn up right now. Excited to increase the speed.

What sort of speed and acceleration figures are you using?

endorphin3d, 2023-10-13:
So my current bottleneck is no longer the physics of the printer but rather the rate at which my hotend can melt filament (I'm not using a volcano hotend) and the rate my part fan can cool the plastic. My acceleration is 3000 mm/s^2 and my infill speed is 120 mm/s but I'd bet can print faster than that if I upgraded my hotend and fans.

SirNukalot, 2023-10-19:
> So my current bottleneck is no longer the physics of the printer but rather the rate at which my hotend can melt filament (I'm not using a volcano hotend) and the rate my part fan can cool the plastic. My acceleration is 3000 mm/s^2 and my infill speed is 120 mm/s but I'd bet can print faster than that if I upgraded my hotend and fans.

Can confirm, i'm using a V6 hotend and it is now safe around 2500 mm/s^2 with wallspeed at 100 mm/s with very good printing quality and no layer shift. Beginning with 3500 mm/^2 the layer shift starts. Also tested only with 0.4 nozzle till now.

Setup:
- endorphin stage3 mod
- original stepper motors
- original mainboard v4.2.2 with TMC2209 stepper drivers
- runs on marlin 2.1.x bugfix
- dragonfly bmo hotend
- 4020 hotend cooler
- 2x5010 part cooling fans

mattswest, 2024-01-15:
I've seen this issue pop up twice in the last few days in the Ender5 subreddit.

I believe some setups will require `#define MARKFORGED_INVERSE` to be set in their Marlin config. It seems this was [added ](https://github.com/MarlinFirmware/Marlin/pull/26516)about a month ago.

This seems like it would be the solution for the issue [powermandan](https://github.com/powermandan) and [SirNukalot](https://github.com/SirNukalot) are seeing.

endorphin3d, 2024-01-15:
@mattswest you're a rockstar! Thanks so much for figuring this out. As I'm not running marlin anymore, is there anyone who's able to confirm if this fix works?

mattswest, 2024-01-16:
Unfortunately the [PR](https://github.com/Klipper3d/klipper/pull/6321) for similar functionality on Klipper seems to have stalled out.

I checked the Discourse but it looks like no one followed through with it.

endorphin3d, 2024-01-16:
Well I've never had an issue with Klipper and I think it's because of these two lines in my config:

```yml
position_endstop: 0
position_max: 220
```

I'll need to update the docs for that

Closed 2025-01-11.

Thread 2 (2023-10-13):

Stage 3 - Missing EVA STL file

TristanPeers, 2023-10-13:
One of the EVA STL's is missing for [stage 3]( https://github.com/endorphin3d/endorphin/blob/main/docs/stages/stage-3.md )
The link to this STL is missing ->   [eva-endorphin_belt_grabber.stl](https://raw.githubusercontent.com/endorphin3d/endorphin/main/STLs/stage-3/eva-endorphin_belt_grabber.stl)
It is also not present in the repo, there are only 2 EVA stl's here -> [https://github.com/endorphin3d/endorphin/tree/main/STLs/stage-3](https://github.com/endorphin3d/endorphin/tree/main/STLs/stage-3)

Please can you add this file or advise where I can get it? Many thanks

endorphin3d, 2023-10-13:
Good catch, the file should be present now. Sorry about that.

TristanPeers, 2023-10-13:
Awesome - thank you so much!

Closed 2023-10-13.

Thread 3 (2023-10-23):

EVA system not quite compatible with Endorphin

TristanPeers, 2023-10-23:
Hi - the EVA system is not compatible without some modification (sadly the setup you have listed does not work as is).

Firstly many thanks for creating this system!!!

I did stage 1 first a few weeks back and everything was working fine. I changed the kinematics to `hybrid_corexy` - all good. I printed all the parts for stage 2/3 and EVA on this new setup - no issues.

I've just tried to do stages 2/3 with the EVA carriage this weekend.

Sadly the first problem is that X became reversed. I changed the X `dir_pin` to fix this, but then when you move Y, X also moves at the same time.

This is exactly the same as this person reports (see my comments): https://www.reddit.com/r/ender5/comments/169eomj/endorphin_y_motion/

The problem is that the belt attachments for the EVA setup with Endorphin are on the [back](https://github.com/endorphin3d/endorphin/blob/main/docs/stages/stage-3.md?plain=1#L97-L101). As you can see from the Reddit thread above the person has decided to update his `hybrid_corexy` python code to combat this.

I have opted for the simpler approach of moving the belt attachment to the front however the EVA front attachment with the current Endorphin parts cause the belt to rub.

Just thought I'd let you know.

endorphin3d, 2023-10-23:
Ok, I think I know the issue you guys are facing because I ran the EVA for a good while without any issues. I think rather than inverting the pin, you need to tell Klipper the endstops are on the other end (200 rather than 0). Here's my Klipper config for X and Y:

```yml
[stepper_x]
step_pin: PB9
dir_pin: PC2
enable_pin: !PC3
microsteps: 16
rotation_distance: 40
endstop_pin: ^PA5
position_endstop: 220
position_max: 220
homing_speed: 50

[stepper_y]
step_pin: PB7
dir_pin: PB8
enable_pin: !PC3
microsteps: 16
rotation_distance: 40
endstop_pin: ^PA6
position_endstop: 200
position_max: 200
homing_speed: 50
```

If you do this with the belt on the back and this fixes things, I'll update the docs that `position_endstop` should be `200`.

TristanPeers, 2023-10-23:
Hi - sorry, that's not the issue. My config is pretty much identical to yours and my endstops are also on the end of the axes (position_max):

```ini
[stepper_x]
step_pin: PB9
dir_pin: PC2
enable_pin: !PC3
microsteps: 16
rotation_distance: 40
endstop_pin: ^PA5
position_endstop: 220
position_max: 220
homing_speed: 50
homing_retract_dist: 0

[stepper_y]
step_pin: PB7
dir_pin: PB8
enable_pin: !PC3
microsteps: 16
rotation_distance: 40
endstop_pin: ^PA6
position_endstop: 190
position_max: 190
homing_speed: 50
homing_retract_dist: 0
```

This config above is what I had running with stage 1.

As soon as I installed the EVA carriage (with the belt attached on the back) and turned the printer on with the config above, X was reversed. It tried to home on the left of the printer. And the X movements were reversed in Fluidd. Pressing right in the console moved the carriage left and vice versa.

As X was now reversed, I changed it to:

```ini
[stepper_x]
step_pin: PB9
dir_pin: !PC2
...
```

And X behaved correctly....however when moving Y, it also moves X at the same time.
Moving the belt attachment to the front has fixed the issue (keeping the config above, not the inverted `dir_pin`)

endorphin3d, 2023-10-23:
Okay I see. As I now am running the Vz printhead with the belts at the front, I don't know exactly what my config looked like when I had the EVA, but I'm curious what would happen if you changed the X settings to the following:

```yml
[stepper_x]
step_pin: PB9
dir_pin: PC2
position_endstop: 0
position_max: 220
```

TristanPeers, 2023-10-23:
The endstop position is just telling klipper where the microswitch is located.

As per the discussion I posted [here](https://www.reddit.com/r/ender5/comments/169eomj/comment/k5yaqto/?utm_source=share&utm_medium=web2x&context=3) it doesn't really have any effect for this problem.

...and the X motion would still be reversed.

You could recreate the issue yourself by attaching the belts to the back of your Vz instead of the front to mimic the EVA.

endorphin3d, 2023-10-23:
Ok so I switched my belts to the back and changed my X settings to the ones I recommended and it works just as expected--X moves as I step it, Y moves as I step it, and there's no unnecessary movement from one when I move the other. I'd recommend trying those X settings I mentioned.

TristanPeers, 2023-10-24:
Thank you for trying, but I think I'm just going to stick with the front attachments. It's simple, the endstops are in the default location and everything works as intended.

As per the other person, they [said](https://www.reddit.com/r/ender5/comments/169eomj/comment/jz3eyml/?utm_source=share&utm_medium=web2x&context=3):

> I changed the position_endstop for X to zero and no[sic] Y moves correctly but that creates a new problem.

I've no idea what the other `new` problem is they mention but unfortunately I don't have the time to keep switching the belts to `experiment`. I really need a stable system, this is my only printer and due to the location of the front attachments in EVA I have to fully strip the carriage to access them. That means doing all the wiring, fans, extruder, redoing BLtouch, resetting XYZ offsets and also using different belts.

I'm just going to remix either the EVA front or your Endorphin right rail mount in a few weeks time. I've just cut/sanded off the corner of the Endorphin rail mount for now to stop the belt rubbing.

Perhaps you can find out what the other problem is? I'm guessing something to do with prints being reversed.

roastcuprepeat, 2023-11-26:
I can also confirm that modification needed in klipper/klippy/kinematics/hybrid_corexy.py

endorphin3d, 2023-11-26:
@roastcuprepeat did you happen to mess with `position_endstop` for both stepper_x and stepper_y? I'm trying to pin down exactly what the variable is here, because I ran the EVA printhead just fine without any modification to the `hybrid_corexy.py` for quite some time.

There's four possible combinations for position_endstop:

1. Set to 0 for both x and y
2. Set to the max for both x and y
3. 0 for x, max for y
4. Max for x, 0 for y

I'm now running the Vz printhead with the belt attached at the front, and both my x and y are set to the max (220 and 200 respectively). I'm guessing that some combination other than that will yield you a working kinematic without having to touch the .py file.

roastcuprepeat, 2023-11-27:
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

@endorphin3d Currently I 'm runnning x and y endstop at max position, dir pin is reversed from the original config.

endorphin3d, 2023-11-28:
@roastcuprepeat If you're willing, I'd love to know what the printer does when you do the following:

1. Set the direction pins back to the original
2. Set the x `position_endstop: 0`
3. Leave the y endstop set to the max
4. Undo your changes in the .py file

I just did this on my printer and it moved correctly for a printhead where the belts attach at the back rather than the front.

roastcuprepeat, 2023-11-29:
@endorphin3d

Unless my understanding is wrong I think we have to reverse the direction pins.
However I'll try more test when i have more time this weekend because I really don't want to touch the hybrid_corexy.py

roastcuprepeat, 2023-12-04:
@endorphin3d Sure. Sorry didnt have time last weekend but definity will test and report back.

roastcuprepeat, 2023-12-05:
@endorphin3d

1. I switch back to the original hybrid_corexy.py
2. Set the direction pins back to the original
3. Set the x position_endstop: 0

with G28 X0, X home to the switch.
Y moves without moving X
but now the coordinate is mirrored on X?
now I have (220,0)at bottom left.

endorphin3d, 2023-12-06:
@roastcuprepeat Thanks so much for the info--I knew there was some tradeoff to this but I couldn't remember what it was. You can actually change the print origin in your slicer to match the printer. This is what my settings look like in OrcaSlicer. You could play with both X and Y to see what fits your printer.

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

roastcuprepeat, 2023-12-06:
@endorphin3d This setting doesnt let us to mirror the axis, however in theory if I reverse the dir pin of y i can get a 180 degree rotated bed.

ambarusa, 2024-12-16:
@roastcuprepeat I am really curious if there has been any solution to this, before diving into this stage. Could you fix this?

endorphin3d, 2025-01-11:
To anyone using the Eva printhead, I just updated the STEP file to include the Endorphin-modified Eva printhead

Closed 2025-01-11.

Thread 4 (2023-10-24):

Replace cantilevered bed?

kozross, 2023-10-24:
Is there any chance there could be a stage 4 to fix the bed being cantilevered? On a bed size this large, this is a _significant_ downside.

endorphin3d, 2023-10-24:
Believe it or not, that was exactly what I had in mind for stage 4. Here's a preview of what I had in mind:

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

Unlike similar projects I've seen on Thingiverse, it will only need one new rail and one new lead screw--either driven by a belt or by a second motor (there's tradeoffs for both and I'd love some opinions on which to pick). I've been busy with other work lately but if you or anyone else has the CAD skills to work on this, I can upload what I have so far.

kozross, 2023-10-24:
Basically, dual-motor is always better unless you lack the steppers on your board. Belt sync is _OK_, but it's always going to be second-best, especially given that this bed is fairly large. I think the stock board _may_ have dual-Z capability, but I'm not sure, so I'd say unless budget is a major concern, prefer two motors.

I definitely lack the CAD skills, so I'll wait patiently.

endorphin3d, 2023-10-25:
Yeah, it doesn't look like the stock boards have the second Z plug. The other upside of a belt is the two lead screws always stay in perfect sync and you don't have one side sag when the steppers are off (I've seen this happen personally).

kozross, 2023-10-25:
That's true, but to be honest, I'd probably replace the board with something like an M5P anyway, which _does_ have enough Z connections. The downside of a timing belt is that it has to be of a _very_ precise length (as you can't tension it), and thus, it's quite unlikely you'll find one in the right size without special ordering. A second motor and a board with dual Z steppers, however, is much easier to get hold of.

As someone who's had a timing-belt-linked Z printer, I can tell you that this kind of sag can happen there as well, and it's _much_ harder to fix. There's multiple printers without timing belts that solve this problem by literally crashing themselves into the ceiling (Prusa MK3, Sovol SV06, probably some others I'm forgetting), which I think that this printer would be capable of (assuming it has TMC2209s in it).

At the very least, I would prefer having the option to dual-Z, with or without a belt. Single-drive Zs have given me issues with far smaller and less heavy beds in the past.

TheRealGennie, 2023-12-21:
My addition would be to delete or reposition the 2 shorter 2020 extrusions holding the z gantry (is that the correct term?), moving the gantry 20 mm further back, making room for a larger bed. With a narrower x gantry (due to rails instead of the wheels) that could make a great solution

endorphin3d, 2023-12-21:
@TheRealGennie that's a fantastic idea actually. Someone on Reddit recently [posted](https://www.reddit.com/r/ender5/comments/18chfdk/first_draft_on_ender_5_dual_z_project/) a dual Z project which didn't have the goal of enlarging the bed, but he did end up removing that 2020 extrusion extrusion and made his own adapter plate.

So to everyone in this thread, do we want to make dual Z _and_ larger print area the goal of stage 4? Just one tradeoff here: If we go down the path of having printed bed supports, that basically rules out the future possibility of adding an enclosure because those printed parts will sag.

kozross, 2023-12-21:
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

I don't think the bed needs to be any larger honestly. One of the things that appeals to me about the Endorphin is that it's quite simple and makes minimal changes. A bed size mod feels entirely outside of that scope.

wildstar87, 2025-03-25:
I'm interested in having the mounts on the outside, at least on the front, to not lose build space, but options to move both to the outside would be nice as well.

Regarding the dual motor z, I happened to notice, after replacing the X-axis, with the extruder motor, that the old x-axis stepper is the same stepper as the existing z-axis stepper.  Since I went to the Sprite SE extruder, the old extruder mount (w/o extruder parts), is essentially the same mount that is used to mount the z-axis stepper as well.

There is also this reddit post on adding a second z-axis driver to the Creality 4.2.2 board:
https://www.reddit.com/r/ender3/comments/qzxleg/i_added_a_5th_stepper_driver_to_the_stock/

So with minimal work, and just duplicating the BOM of the existing z-axis parts, a dual adjustable motor z-axis, seems to be fairly easy to do.

I know this would be extra cost, but I also found this plate on thingiverse, that could be sent out to online CNC services
https://www.thingiverse.com/thing:4677103.  That essentially does just that.

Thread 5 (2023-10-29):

Ender 5 Plus-specific build plan/issues

tryptech, 2023-10-29:
Started working on implementing the Endorphin mod on my own Ender 5 Plus (E5P) and will document my findings and any potential issues here.

# Stage 1
This stage can proceed with no changes relative to the Ender 5 (E5) version.

# Stage 2
The usual linear rails used for E5P modification, notably the Fabreeko Mercury One.1 kit and the 3DFused Linear Rail kit, are 450mm millimeters in length so I will plan on using MGN12H at that length.

The left linear rail mounting will likely be fine. The E5P uses 2040 extrusion for more of its frame than the E5 so a different jig should be suggested/used.

The right linear rail will have a problem. The E5P uses two lead screws on the left and right of its bed in order to drive Z motion. The corners are guided by steel rods at each corner. These rods are fixed to 2020 extrusions that are connected to the side 2040 extrusions. If the right rail is mounted on the inside, the carriage would intersect with the 2020 extrusion below it, assuming the carriage has the standard width of 27mm. E5P linear rail mods only mount on the top or outside of the 2040 extrusions for this reason. Thus the mounting would have to be adjusted to other side of the extrusion.

# Stage 3
As is the case in stage 2, for standardization with other E5P mods, I intend on using another 450mm MGN12H rail.

If possible, I want to find a top mounted rail Afterburner/Stealthburner mount since I have a printed and working shroud + toolhead and would prefer to avoid buying parts to build a new printhead. That is to be determined before I proceed with this stage.

tryptech, 2023-10-30:
Stage 1 has been implemented relatively fine without a hitch, but I'm concerned about the relocated X motor. When moving along the Back-Left to Front-Right diagonal, the motor seems like it is at it's operating limit at ~160mm/s. This seems to be the case for both the 42-34 and the 42-40 motors.

The following videos are taken with the 42-40 motor in place.

https://github.com/endorphin3d/endorphin/assets/654389/c4334c4e-0964-44ba-bcb6-228cdd0e9e8d
https://github.com/endorphin3d/endorphin/assets/654389/edc848d4-d520-4fa6-bf88-27bb78abbed3

When moving along the Back-Right to Front-Left diagonal, the motor doesn't move in comparison.

https://github.com/endorphin3d/endorphin/assets/654389/2c2f52a2-671f-461f-adf0-ca2f36734391
https://github.com/endorphin3d/endorphin/assets/654389/1aeaa620-20c5-4bcf-8a20-1bf05b6a7c34

For now I've implemented a maximum speed of 150mm/s. This ends up being a downgrade to how I had my printer before relocating the motor. There I had an operating limit of ~185mm/s on Y-axis moves, with X-axis moves having a significantly higher limit.

endorphin3d, 2023-11-06:
Thanks so much for taking time to write this detailed review @tryptech. Are you seeing skipping on the X motor, or what are the signs you're seeing for the limit being ~160mm/s?

As for the rails causing collisions on stage 2, would 425mm rails solve the problem?

tryptech, 2023-11-06:
I don't believe the issue to be skipping, doesn't sound like it. I think the wheels aren't keeping up and are dragging and running on the extrusion. At least, that's what it sounds like. Other E5Ps can go faster than mine, so I'm chalking it up to these wheels being worn enough that they aren't suited for the task anymore.
I'm going to proceed with stage 2 and 3 soon enough to leave the wheels behind, so it likely isn't a huge issue, but enough to note that a well tuned E5P may not necessarily see any speed benefits from stage 1. I expect Input Shaping and accelerations to have better results due to less mass being thrown around though. More time spent at top speed may be enough of a gain to justify Stage 1 for any E5P users who already have pushed the stock configuration as far as they can.

The issue with the linear rail isn't the length of the rail, it's the width of the carriage. If you take a quick look at the [4020 extrusion on the top sides](https://grabcad.com/library/creality-ender-5-plus-1) you can see a 2020 extrusion attached to it on the lower inside part for the lead screws and steel rods. This poses an issue with mounting the rails on the inside because the nominal width of an MGN12H carriage is 27mm. No way it can fit at all. Hence the mounting needing relocation on the outside. 450mm should work fine as with all other E5P linear rail kits aside from that one core issue.

FilipeThePinho, 2024-05-14:
@tryptech do you still have the same issue with the X motor? And btw, which is the length of the belt you used?

Thanks!

geekyhawkes, 2024-08-12:
@tryptech what size belts did you use for the stage1 5+ update? Thinking of giving it a try but no idea what size belt to order.

LadyArtemis, 2024-10-09:
I'm in the process of making this upgrade now. I am doing all three steps at the same time. some things to note (and likely expected)

- upgrading the Ender 5+ is more expensive than the cost of the Ender 5/pro by approx $27 (liner rails run about $8 more than the ones in the guide. everything else should work)
- the 2040 rails required a different guide for placing the linear rails. I'm using [https://www.printables.com/model/224831-2040-mgn12-alignment-tool but I'm sure that any 2040 guild will work. ](https://www.printables.com/model/224831-2040-mgn12-alignment-tool but I'm sure that any 2040 guild will work. )
- I'm moving the motor to the back as it is with the standard guide so I will let you know what I see there.
- I am using the Linear rail on outside and linear y switch on rail STLs that are in the issue linked above.

Things I know will need to happen without even installing anything
- The klipper settings will need to change to
`[stepper_x]
...
position_endstop: 360
position_max: 360

[stepper_y]
....
# Note: These may need to be 340 if using the EVA printhead
position_endstop: 350
position_max: 350'

I'm going to need to confirm those numbers and I am using the EVA so I will do that.

I currently have parts on order and being shipped so I expect to be able to complete the upgrade in a few weeks.

geekyhawkes, 2024-10-09:
Great thank you! Certainly keen to hear your experience and lessons. I have
linear rails already so cost wise shouldn't be too bad but interested in
the tooth cable length required and any other observations.

Benefits post upgrade will also be of interest!

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

Closed 2025-01-11.

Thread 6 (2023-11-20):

Y tensioner

roastcuprepeat, 2023-11-20:
Hi,

Looking to make a left Y tensioner matching the right,  Could you make one or release the step file so we can edit it?

endorphin3d, 2023-11-22:
I'll try to find time to do this over the Thanksgiving holiday. By the way, the STEP file for this project is already in the repo.

roastcuprepeat, 2023-11-24:
Oh right I missed that.. Made one from the STEP file. Thanks!

jefedahmer, 2024-03-30:
> Oh right I missed that.. Made one from the STEP file. Thanks!

Are you willing to share the stl file?

Closed 2023-11-25.

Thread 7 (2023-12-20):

Placement of the rails, stage 2

TheRealGennie, 2023-12-20:
This mod looks very interesting, and Im planning to go this way. I do have a question (or probably a lot ;)

Why not put both rails on the outside of the frame?

My thinking is that it would increase the possible gantry travel by 50 mm.
My plan is to add dual z (stage 4;) ) move the exixting z axis back, either to the main frame, which would give 20 mm, (or maybe even to the outside of the frame) and the standard hotend assembly have another 12 mm clearance to the front extrusion, This would allow for a larger bed.

endorphin3d, 2023-12-21:
@TheRealGennie Thanks for your interest in the project. I'll paste my answer to the same question from another user on Reddit (I need to add this answer to the docs, as obviously it's a common question)

> The reason the rails are like that is because of the asymmetrical tension the belt puts on the bearing blocks. A CoreXY has two belts, each pulling in opposite directions, so this isn't an issue. But on the Endorphin I wanted the belt tension to be pulling the bearing blocks toward the rail rather than away from it. If you look at a bearing block up close, I don't think it would take too much strength to rip it off a rail.

Maybe I should make a version of the right rail mount for users who want to put both rails on the outside. Personally, I would be curious to see how well a rail block stands up to the tension pulling it away from the rail. I may be fretting over nothing.

By the way I'm really hoping to find some time over the holidays to work on stage 4. Still open to suggestions on stage 4 if you'd like to weigh in here: https://github.com/endorphin3d/endorphin/issues/4

TheRealGennie, 2023-12-21:
Thanks for the answer. I really like this project!!
Im not an engineer, but I did study to be one for a year a LONG timer ago, so I remember a bit about forces. Anyway, (to me anyway) tension is the exact reason to put the rails on the outside. Belts cant push, only pull!! As they cross the middle of the printer, they can never push a bearing block away from the frame, only pull towards it, or towards the steppermotor. Hope it makes sense!! I tried to draw/speak through my thoughts in Explain Everything (https://expl.ai/3MFKKQV) if you are interested

endorphin3d, 2023-12-21:
Hey @TheRealGennie, thanks for the explainer video. The tension I was talking about actually wasn't due to the stepper moving the belt, but the tension that's on the belt 24/7 due to the belt feeding around the tensioner on the left side, but not having a similar belt feeding around a tensioner on the right side of the bed. See the yellow arrow:

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

But like I said, while the tension is there (you can pluck on the belts to feel it) it may not be _near_ enough to matter. I am a big fan of making the print area larger, so this may be worth doing.

tryptech, 2024-01-04:
Adding 2 cents, rail on the outside is exactly what is needed for Stage 2 on Ender 5 Plus as described in #5

endorphin3d, 2024-02-03:
And here's an [STL](https://github.com/endorphin3d/endorphin/blob/outer-rails/STLs/stage-2/linear-y-switch-on-rail.stl) for a Y limit switch holder that mounts in any of the rail's screw holes (with a T nut on the inside, same as all the other T nuts that mount the rail to the frame).

tryptech, 2024-02-03:
I'll give it a go this weekend and report back.

tryptech, 2024-02-05:
Two issues of note with the outside-mounted right-y-rail:

1. 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 Using the M5 bolt to mount extrusion to the part does not account for the space the head of the bolt takes up. The rail carriage is right up against the underside of the part, but the head of the bolt prevents it from sitting flush with the underside and making it impossible to screw in. I worked around this for now by installing an m5 heat set insert on the part and using a an M5x25 bolt from the top.

2. 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 The vertical alignment of the belt ends up hitting the rail with or without the bottom part. I will print the part at half height which should account for it.

sgayol, 2024-02-14:
" Using the M5 bolt to mount extrusion to the part does not account for the space the head of the bolt takes up. The rail carriage is right up against the underside of the part, but the head of the bolt prevents it from sitting flush with the underside and making it impossible to screw in. I worked around this for now by installing an m5 heat set insert on the part and using a an M5x25 bolt from the top."
And now I know why my AliExpress rail kit ended up lifting the X gantry about 6mm.
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

endorphin3d, 2024-02-14:
Yep, I see the issue now. Thanks to both of you for testing. I'll try to design a fixed version this evening.

endorphin3d, 2024-02-15:
Okay, tell me if [this](https://github.com/endorphin3d/endorphin/blob/outer-rails/STLs/stage-2/right-linear-y-outer.stl) one works better. It now uses the inner M5 screw hole to mount to the X rail.

endorphin3d, 2024-02-15:
Okay @sgayol and @tryptech, let's see if [this](https://github.com/endorphin3d/endorphin/blob/outer-rails/STLs/stage-2/right-linear-y-outer.stl) one works better. It now uses the inner M5 screw hole to mount to the X rail.

sgayol, 2024-02-15:
> Okay @sgayol and @tryptech, let's see if [this](https://github.com/endorphin3d/endorphin/blob/outer-rails/STLs/stage-2/right-linear-y-outer.stl) one works better. It now uses the inner M5 screw hole to mount to the X rail.

Printed and installed. Fit is excellent. The only issue I have is that the tensioner I had for the x axis belt needed to be modified. Do you have one that's definitely compatible? It's incredibly helpful having one, especially with the longer belt path.

endorphin3d, 2024-02-17:
@sgayol What do you need to modify about the X tensioner?

sick4noise, 2025-01-01:
Thanks for all of your effort on this. I'm in the process of converting my E5 Plus.

I have another suggestion. With a bit of tweaking of right-linear-y-outer.stl, you could print this in on its side for better strength. It would also require less support. For example:
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

And with some chamfers on those edges you could potentially eliminate any need for supports.

DaKue77, 2025-01-01:
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

Out of the same reason I did this for my Ender 5 Pro outer rail:
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

Shonky-Donkey, 2025-01-02:
I'll throw my hat into the ring here. This is what I came up with:
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

Haven't actually printed and tested this one yet though. Still waiting on parts to arrive on the slow boat from China for my build.
[linear-y-mount-right-ext.zip](https://github.com/user-attachments/files/18291804/linear-y-mount-right-ext.zip)

lastinfantry, 2025-01-18:
> Haven't actually printed and tested this one yet though. Still waiting on parts to arrive on the slow boat from China for my build. [linear-y-mount-right-ext.zip](https://github.com/user-attachments/files/18291804/linear-y-mount-right-ext.zip)

Did you have a chance to test your version already? I really like the approach. Probably going to print it next week.
Did you also model a  matching alternative part for the left side, with the fillets and all?

Shonky-Donkey, 2025-01-18:
I had already printed a version prior to this, which I decided was good enough, but the only differences with the one I uploaded was the gussets, and that I had taken the corner opposite the end stop striker off.

I have no reason to believe it wouldn't work, and I would print the gusseted one if I did it again. The only thing I would add before I printed it, would be a zip tie hole, or other feature to route the x end stop harness through.
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
sick4noise, 2025-01-30:
Turns out I just need to increase the frequency range of the test. Then I found the dominant resonant frequency for the X axis:
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

I'm going to try the recommended shapers and run some tests but this looks promising.

sick4noise, 2025-02-03:
Spent all weekend trying to fix all of the input shaper issues and finally got to a good state. Apparently the first X belt I cut had a slight kink in it that was causing it to bind on the idler. It also took a few iterations to get the X belt lined up and even all the way around. I ended up stacking washers under the idlers to get the right height (could be replaced with a thinner version of the idler bottom).

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

After lots of tuning I was able to increase my acceleration to 6500 without ringing. Above that I start losing steps in the X motor, but I haven't tried increasing current as I don't have the specs on that motor. Though I've got five spares so at some point I'll will tinker with it. For now I'm quite happy with the performance. I printed a Benchy in 32 mins last night which would have taken ~60 mins with Klipper prior to this upgrade.

Having the rails on the outside seems to work well and I haven't lost any bed space. Since the X axis effectively fixes each of the linear rod mounts in the X direction I don't see how X belt could pull on the right linear rod carriage.

Thanks for all of your work on this! It's a wonderful contribution to the community.

endorphin3d, 2025-02-09:
@sick4noise thanks so much for testing this. So are you saying the groove in this new outside mount needs to be cut a little deeper so the X gantry sits a bit lower and you won't have to stack washers?

sick4noise, 2025-02-09:
@endorphin3d Yes, that could address the issue. Alternatively, you could print a thinner version of the center-idler-bottom.stl model and use that in place of the washers.

endorphin3d, 2025-02-10:
@sick4noise are your rails vertically centered on the extrusion? You can check using calipers or you can print a rail alignment tool like [this](https://www.printables.com/model/450861-mgn9-mgn12-linear-rail-2020-alignment-tools)

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

sick4noise, 2025-02-17:
Yes - I printed a rail alignment tool when I installed them.

wildstar87, 2025-03-07:
Is the outer rail mounting for the right rail finalized?  I'm looking at doing this mod, and going straight to Stage 2.  Is there a difference in the BOM between this, and the one on the main doc site, as it seems to only list the older inner rail mounting.

endorphin3d, 2025-03-08:
@wildstar87 we're just doing final tests now. You can get the files now on this [branch](https://github.com/endorphin3d/endorphin/tree/v1.1/STLs/stage-2). I just want to make extra sure the rail blocks still look fine after having the belt tension pull on them for at least a month.

wildstar87, 2025-03-30:
I printed both of the x-axis mounts on their sides, and used the original screws to secure them to the extrusion, and they ended up cracking right at the screw hole, both right in the center.  I think it was because of the depression in the screw hole, and screw head being larger than the depression, so when tightening it down, it flexed in the depression causing the crack, and it traveled right now the layer line, and cracked one of them clean through the middle.  I think it would be better to have this hole just be flat, instead of having that depression for a screw head, so the pressure is distributed evenly, or even a larger washer could be used to disperse the pressure over a larger surface area.

I think printing them where the top area for the extrusion is facing the bed would solve part of this, but create another problem, especially with the right mount, as there is really nothing holding the 90 degree, other than that one layer, which is very thin.

I think probably the best way to print for strength was the first example, where it is printed on it's end, with supports under the 90 degree portion.

ambarusa, 2025-04-12:
@endorphin3d just completed stage 2 with the outer rails. Everything turned out great using the default orientation in the slicer (one of the sides + supports). A quick observation: it would be ideal if the Y-endstop could be adapted to this version in a way that allows the back to support the rail instead of the 2020 profile.

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

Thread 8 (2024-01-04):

clearance to acrylic enclosure

zCruuz, 2024-01-04:
Hi,

since i saw the post regarding this on reddit i am curious to build it. Since back in the day i build a stupid Acrylic enclosure (https://www.thingiverse.com/thing:4314001) , i only have limited space.
Can you provide measurements or cad data for each step? I don't wanna get all neccessary parts just to realize, it won't fit.

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

endorphin3d, 2025-01-12:
Hey @zCruuz just cleaning up some issues. Did you ever get your question answered? The STEP file in the CAD folder should have everything you need.

zCruuz, 2025-01-13:
yes, took me some time to finally do the conversion. In the end i needed to dremel away parts of the enclosure to get proper access but nothing to bad.
Went for a HMG7 with Phaetus Rapido UHF and relocated the front aluminium extrusion.
Usable print bed size is now around 205mm since the Radpio sticks out quite a bit more than the stock mk8.

Next step will definetly be a bigger or relocated heatbed with active chamber heating.

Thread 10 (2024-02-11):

Y motor skipping

Killerherts, 2024-02-11:
I am having issues with the y motor skipping steps when I make directional movements. I am up to stage 2 for the mod.
I have tried ever variation of belt tightness i could think of.

Did you need to change the vref for the motors?

One other thing i ran into with the mod was not having any belt clips printed with the rest of the parts. We should really reference the gt2 belt clips on stage one so users can preprint this when they are printing the mounts for the rails.
I ended up with a belt i couldn't mount without running to the store for zipties

Killerherts, 2024-02-11:
Issue were with linear rails no being lubed

Closed 2024-02-11.

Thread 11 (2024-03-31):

Tension

Jonryux, 2024-03-31:
I am having a issue. Have been in days trying to figure out why the belts are not synced...

I am on stage 1 and used the extruder stepper as X axis.

The problem is like it makes a some kind of sound, maybe am missing steps or like everything is not really sync. I have been trying the tension on belts in different ways but still having trouble on the cube calibration.
Here are reference pictures
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

endorphin3d, 2025-01-11:
That just looks like skipping to me. Try increasing the voltage on the X stepper a bit.

DaKue77, 2025-01-11:
Also make sure steps/mm are correct for the motors.

endorphin3d, 2025-01-29:
@Jonryux I was finally able to reproduce a similar issue, but it was only happening on a small circular part. This seemed counterintuitive to me because larger prints have longer travels to give more time to accelerate which would lead to a higher top speed. I messed with stepper current, `max_accel`, `max_velocity`, `minimum_cruise_ratio` and nothing seemed to do the trick.

After some googling I found people having issues with Arachne causing skipping on curves. I changed my slicer wall generator to "Classic" and the problem was solved. Let me know if this helps you too.

endorphin3d, 2025-02-14:
@Jonryux I just want to follow up on this. I was still able to create skipping when I increased travel speed. I played with the torque settings a bit to no avail, then I found [this page](https://www.klipper3d.org/TMC_Drivers.html) in the klipper docs. Basically, it seems stealthchop is the main culprit here.

> Tests comparing modes have shown an increased "positional lag" of around 75% of a full-step during constant velocity moves when using stealthChop mode

Then there's an additional potential cause:

> The TMC driver interpolate setting may reduce the audible noise of printer movement at the cost of introducing a small systemic positional error.

The solution is in the doc if you read on:

> For best positional accuracy consider using spreadCycle mode and disable interpolation (set interpolate: False in the TMC driver config). When configured this way, one may increase the microstep setting to reduce audible noise during stepper movement. Typically, a microstep setting of 64 or 128 will have similar audible noise as interpolation, and do so without introducing a systemic positional error.

So that's what I did and I'm able to achieve _significantly_ higher acceleration and travel speeds now. It's only _slightly_ louder when printing--mostly during long high speed travel moves--but it's not bad at all.

Here's my stepper config now (this is for an SKR mini v3). If you have any `stealthchop_threshold` lines in your config, delete it.

```cfg
[stepper_x]
...
microsteps: 128
...

[tmc2209 stepper_x]
...
run_current: 0.620
interpolate: False
...

[stepper_y]
...
microsteps: 128
...

[tmc2209 stepper_y]
...
run_current: 0.650
interpolate: False
...
```

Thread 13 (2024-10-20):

Endorphin on Ender 5 plus

Stenli37, 2024-10-20:
Hi. I did stage 1 and 2 simultaneously and will do stage 3 eventually. So I got MGN12H 450mm linear rails and 5 meter belt, everything else stayed the same as in the guide. Firstly, I printed all the parts without any changes, but after disassembling everything I discovered that the rail doesn't fit on the right inside because of the Z-axis rods being mounted to an additional side rail/gantry.  So I removed it and the printer worked ok enough to print a modified version of the y mount (https://www.thingiverse.com/thing:6803371/files) (idk how to upload stl files here, sorry). I have it printed and everything fits nicely. Other than that, I didn't move the endstops, since there was no need to.  I will upload some vids later.
As for the firmware, I used this - https://github.com/InsanityAutomation/Marlin/tree/CrealityDwin2.0_Bleeding with this config, because I can use my stock screen, without any changes https://github.com/MarlinFirmware/Configurations/tree/bugfix-2.1.x/config/examples/Creality/Ender-5%20Plus/CrealityV1%20(RELOADED%20UI). In the marlin config file I had to enable the inverse markforge otherwise the printhead would just run in the opposite direction.

#define MARKFORGED_XY
//#define MARKFORGED_YX
#if ANY(MARKFORGED_XY, MARKFORGED_YX)
 #define MARKFORGED_INVERSE  // Enable for an inverted Markforged kinematics belt path
#endif

sick4noise, 2024-12-27:
@Stenli37  Can you post a pic of your modified Y-mount on Thingiverse? I'm interested in using it for my E5P but not quite sure how it mounts.

Shonky-Donkey, 2024-12-31:
> @Stenli37 Can you post a pic of your modified Y-mount on Thingiverse? I'm interested in using it for my E5P but not quite sure how it mounts.

Something like this, I suspect:
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

sick4noise, 2024-12-31:
> > @Stenli37 Can you post a pic of your modified Y-mount on Thingiverse? I'm interested in using it for my E5P but not quite sure how it mounts.
>
> Something like this, I suspect: ![image](https://private-user-images.githubusercontent.com/88253304/399400897-09c0e0dc-ecf5-426a-9892-a40f56868adc.png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)

It seems so obvious now :) Thank you!

Stenli37, 2025-01-07:
Hey, finally finished the stage 3. It took me some time, since I converted to mircoswiss direct drive and had some trouble finding a linear rail mod for it, together with a new printhead. Attached is a video of the final thing and a picture of the y-mount, as requested above.
So for the linear rail I used this - https://www.thingiverse.com/thing:5002103 - no additional modifications, didn't move the y-endstop.
For the printhead - https://www.thingiverse.com/thing:5178108 - however, there were a couple of things. The connector of the BLtouch on the e5+ is bigger/bulkier, so I had to drill and melt a piece from the "StealthSwiss_mounting_plate_universal" so that it would fit. The top left hole on the direct drive plate, to which the linear rail adapter is mounted, is also covered by this plate, so I drilled a new one. I also had to move the X-endstop to the right a little bit, since the nozzle would start printing the cleaning line a few millimeters off the plate. I did this by trial and error, so I cannot say exactly how much. I also used the y-endstop file from stage 2 to lift the x endstop a little.

Some time ago I bought an x tensioner from aliexpress, which, as I later found out, is normally mounted sideways and is for Ender 3, I think. But anyway, I managed to make it work - had to melt a bit of the corners from the endorphin mount and also use 3 washers to fill the empty space between the rollers on the mount. I will probably buy/make a better one in the future.

I know the belts on the y-axis should go under the mount, but I found that out much later and am now too lazy to disassemble everything.

The other mods I have:
https://www.thingiverse.com/thing:4825660 - bracers
https://www.printables.com/model/116582-ender-5-plus-crossbar-variable-relocator - crossbar relocator
https://www.thingiverse.com/thing:4871661 - toolholder
https://www.thingiverse.com/thing:4255482 - cable guide tower
https://www.thingiverse.com/thing:4165428 - bed cable strain relief

I have also prepared some of the bed spacers from here, just in case if my bed wasn't high enough for the nozzle-
https://www.printables.com/model/563494-ender-5-micro-swiss-dd-linear-rail-adaptor/files

Also, if you convert to direct drive don't forget this, very useful -https://www.thingiverse.com/thing:3593964

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

https://github.com/user-attachments/assets/ca2d533a-16fd-49e7-885e-afe3b562dd1a

endorphin3d, 2025-01-11:
Thanks @Stenli37 for all the info! I think that `MARKFORGED_INVERSE` line was what's been missing for people using Marlin so I added that to the docs. I'm going to close this issue and let the convo continue on issue #14 about putting the benefits/drawbacks of putting rail on the outside on the E5+.

Closed 2025-01-11.

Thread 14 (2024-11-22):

Endorphin on a 5+ HIGHLY recomended

GarthyJBI, 2024-11-22:
Well i cant reccomend this upgrade enough for the 5+

I have wanted to upgrade my machine with linear rails since I got it in March but just havent got around to it but the more hours it did the more those stupid wheels were wearind away and just leaving mess everyxtime I did a print and the amount of adjustzments I had to do everytime before I set of a print was just getting on my nerves so I looked around for an upgrade and came across this recomended in a Reddit post.

So i looked at the cost and figured it was worth a try cause apart from the linear rails which I was going to need no matter what I did I had practically everything else laying around from tinkering with 3d printing over the years just bought a 10m belt and the rails and away I went.

There are some differences between doing this on a 5 and a 5+ the main one being when fitting the right side linear Y axis rail the stabilisers for the bed are bolted to the frame and so you cannot fit the rail so I decided to just unbolt them and they are sturdy anywaysd so didnt bother finding a way to reattach them.

I also decided that for now to keep costs right down I didnt want to do a hotend upgrade so printed a new fan peice for the original hote end and found a linear rail holder for it on thingiverse and so far so good.

So after running through all calibrations and speed testing Im am currently reprinting a moon lampshade that I printed last week and it took over 58 hours then but now Its at 95% and has only taken 16 hours and the quality is better than the 58hour one.

Thank you very much for the MOD well worth it for such an uprade which takes every little effort and cost.

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

aaron-harvey, 2024-12-06:
I used [this tensioner](https://www.printables.com/model/885298-endorphin3d-ender-5-y-axis-belt-tensioner) and have been pleased with it

Shonky-Donkey, 2024-12-31:
What about this to solve the Z rail issue?
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

[linear-y-mount-right-ext.zip](https://github.com/user-attachments/files/18279010/linear-y-mount-right-ext.zip)

I haven't tested it yet, but it's what I plan to try. I've attached a step file if you want to be the guinea pig.

endorphin3d, 2025-01-11:
Hey @GarthyJBI thanks so much for the tip on unbolting the vertical rail holders. I can add that to the docs if a few other people confirm that it's still 100% stable or I'll accept PR's for anyone who wants to design a replacement that bolts on the underside of the Y rail.
As for the tensioner, I finally got around to adding one. See my comment [here](https://github.com/endorphin3d/endorphin/issues/9#issuecomment-2585400969).

endorphin3d, 2025-01-11:
@Shonky-Donkey great minds think alike. I have a _very_ similar design on a branch [here](https://github.com/endorphin3d/endorphin/blob/outer-rails/STLs/stage-2/right-linear-y-outer.stl). If you'd like to be the tester, let me know.

Stenli37, 2025-01-17:
@johnscrub For the X belt I bought a total of 5 meters length, and I've used 2,4m. So if you buy 3m, you will be good. I kept the Y belts stock, and I suppose they should be good if you put them under the mounts as intended. They aren't long enough if they go above the mount like mine, so I made these "holders" for them, that you can see in the picture/video.
And yes - 3 MGN12H 450mm rails.

lastinfantry, 2025-01-18:
I think you can get away with shorter rails, at least for the X-axis.

I got a really good deal on 350mm rails and I am currently printing the parts for the Endorphin mod (for my Ender 5 Plus). I'll update here sometime next week once I tried installing it with my short rails.

I already have a rail on my X-axis. On the left side I mounted a block on the 2020 extrusion to avoid the train sliding off the rail in case of skipped steps (instead of using the little plug on the screw hole of the rail). On the right side I kept the stock endstop switch, still mounted on the extrusion.
This way I only lost very little print volume despite the short 350mm rail. With 400mm rails you should be able to use the full bed.

But if you have to pay full price, just get the 450mm ones to be sure. This way you can probably mount physical endstops on the rails themselves (mine came with "plugs" for the screw holes) instead of on the extrusions, much cleaner and a little less weight.

endorphin3d, 2025-01-23:
Okay folks, I've listened to the recommendations of a few people in issue #7 and made right-side outer rail mount. Please test and let me know how it works.

[right-linear-y-outer.stl.zip](https://github.com/user-attachments/files/18515231/right-linear-y-outer.stl.zip)

johnscrub, 2025-01-23:
@Stenli37 would you be able to share your config changes n for klipper? I've got stage one done but the docs are only for E5 or e5pro. Thanks

Stenli37, 2025-01-24:
@johnscrub I'm using marlin with stock board and screen. You can see the version and everything in the links in my post.

johnscrub, 2025-01-24:
> [@johnscrub](https://github.com/johnscrub) I'm using marlin with stock board and screen. You can see the version and everything in the links in my post.

Thank you, my GitHub etiquette is not good. I saw way after I posted. I do apologize

johnscrub, 2025-01-26:
Can anyone that is using this on an e5plus and running klipper... Share what changes they made to there cfg? Or there complete printer cfg? Tia

CantElevate, 2025-01-29:
> Can anyone that is using this on an e5plus and running klipper... Share what changes they made to there cfg? Or there complete printer cfg? Tia

https://endorphin3d.com/docs/firmware#klipper

These are all the changes required for endorphin3d in klipper. everything else should be the same as it was before you changed the physical parts of the printer.

I use Klipper, however my setup is about as individual as they come.

The only real difference with the plus in regard to endorphin is the dimensions.

ingramcl, 2025-01-30:
@GarthyJBI would you be able to post the fan and linear rail files you used for the stock hot end.  I am about to make the jump with my 5+ and like you won't be upgrading the hot end just yet.  I am going to start printing the parts tomorrow and the ordered parts should be here soon.  Thanks!

khisanthax, 2025-02-08:
The only changes in klipper were the kinematics line?  I had to swap the pin direction on the y axis but I still get no trigger on x.  Any other changes?

khisanthax, 2025-02-08:
> The only changes in klipper were the kinematics line? I had to swap the pin direction on the y axis but I still get no trigger on x. Any other changes?

I over tightened the screws on the idlers on the x gantry binding movement completely.  I had washers on the tops and bottoms, but assumed that I wouldn't have to worry about over tightening.  I either used the wrong washer or was just wrong about over tightening.

Kikkero, 2025-03-16:
> [@johnscrub](https://github.com/johnscrub) For the X belt I bought a total of 5 meters length, and I've used 2,4m. So if you buy 3m, you will be good. I kept the Y belts stock, and I suppose they should be good if you put them under the mounts as intended. They aren't long enough if they go above the mount like mine, so I made these "holders" for them, that you can see in the picture/video. And yes - 3 MGN12H 450mm rails.

The instructions for stage 3 say to use a MGN9H rail for for the X axis.  Is there a reason why when doing this mod on the E5+ I should go with the MGN12H for the X axis, instead?  I don't know too much about the differences between these rails, but the MGN12H rails look to be a bit beefier than the MGN9H ones and the carriage looks different.  I suppose the beefed up rail would be good for rigidity, but wouldn't this cause problems with compatibility, weight, and/ or clearances?

I have everything here to do stage 1, which I plan on cracking into here in the next few hours, and I have the stage 2 rails on the way.  I'm still waiting to jump on stage 3 until I make a decision on what I want to do with the tool head.  I've already got a Spider 3 hotend and Sprite DD extruder (not the sprite pro kit) installed which are plenty to do what I need (I bought this thing in a state and I just needed a drop-in fix quick with minimal surprises.  The only thing I really (really, really) need as far as the basic toolhead performance goes is better part cooling to keep up with all the extra heat I'm pumping out.  Or am I just completely off base and this configuration will be totally inadequate and become a major bottleneck for me once I'm throwing that head around at the upgraded speeds?  And how will this affect which rail I need (if at all)?

yourzero, 2025-04-03:
> [@GarthyJBI](https://github.com/GarthyJBI) would you be able to post the fan and linear rail files you used for the stock hot end. I am about to make the jump with my 5+ and like you won't be upgrading the hot end just yet. I am going to start printing the parts tomorrow and the ordered parts should be here soon. Thanks!

@GarthyJBI or @ingramcl - Do either of you have these files? I'm in the same boat - going to Stage 3 but with the stock hot end.

Thank you!

CantElevate, 2025-06-13:
When I originally did the stage 3, I went looking for a mount that made things work. this one  seemed to replace the stock mount with one that works with the rail and front connecting belts of the stock motion system

X_Axis_Linear_Rail_Mount_final.stl
https://www.thingiverse.com/thing:3782865/files

CantElevate, 2025-08-26:
> I am looking into the endorphin3d mod for my ender 5 plus. However, I'm not seeing a lot of info on changes to the bill of materials (particularly the rails) for the ender 5 plus. I'm assuming that the BOM specs are for the standard ender 5.
>
> Does anyone have info on the exact changes needed to the BOM for the ender 5 plus?

I used 3 x **450mm** mgn12h rails for my ender5 plus conversion, but knew early that the mercury one.1 was a likely project in the future.  I don't recall any other changes to the Endorphin bom for the conversion.

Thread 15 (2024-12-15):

Stage 3 Linear rail type

ambarusa, 2024-12-15:
Hello,

Before diving into this stage, I would be interested to know what is the reason of using MGN9H type of rail for this rail?
My case is a bit specific, I have an easy access to MGN12C rail, which is the recommended rail type for EVA printhead.

Apart from saving extra weight with MGN9 rail, is there any reason why we should use it?

endorphin3d, 2024-12-15:
MGN9 was chosen simply because it weighs less than the 12. MGN12 should work fine, it's just going to weigh more so your acceleration and jerk settings will max out at lower values.

ambarusa, 2024-12-15:
Makes total sense,I’m fully convinced. It was good though to clarify that it’s not absolutely obligatory.

ambarusa, 2025-03-10:
@endorphin3d FYI, with this approach I bought MGN9C rail type for even less weight, and used the corresponding STLs from VZPrinthead and your custom ones.

_"Make sure you print the MGN9H version of the carriage top (assuming you bought your rails from the links above) rather than the MGN9C version."_ - This note made me afraid that the C type will not be compatible, but so far no issues at all.

Closed 2024-12-15.

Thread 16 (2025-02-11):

tension screw video wrong

lwkalis, 2025-02-11:
The video for installing the tension screw show the m5 going in to the carrier with the nut close to the pulley. when tightening the bolt it runs into the belt. Bolt should be inside and nut should be on the knob.

endorphin3d, 2025-02-11:
Good catch. Thanks for noticing. I'll close this issue when it's updated.

DaKue77, 2025-02-11:
> The installation video for the tension screw shows the M5 bolt being inserted into the carrier with the nut positioned near the pulley. However, when tightening the bolt, it interferes with the belt. To prevent this, the bolt should be placed inside, with the nut secured on the knob.

During my mod I faced the described issue and so I remodeled the knob to be thicker.
@lwkalis , your approach is so much easier and also logically more straightforward! Very good point! 👍🏻

endorphin3d, 2025-05-27:
Fixed in 1.1

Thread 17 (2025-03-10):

Stage 3 X Endstop Solution

ambarusa, 2025-03-10:
Hello,

I am currently assembling stage 3 while temporarily skipping stage 2. However, I’m facing some confusion regarding the X endstop mounting.

The VZPrinthead is designed with a plain switch on the printhead itself, whereas the Ender (including stage 2) does not have a dedicated object to trigger it. Additionally, the original X endstop on the Ender would need modifications to be compatible with the linear rail setup.

The documentation does not mention the endstop installation at all. Could you describe how you mounted the X endstop with your VZPrinthead? It seems like an additional part might be necessary for proper X homing—perhaps something like this:
https://www.printables.com/model/255081-x-endstop-mount-for-linear-rail

Also, if the endstop is mounted on the left side on the printhead as described in the VZPrinthead documentation, then the `homing_positive_dir: `setting for `stepper_x` should be set to `true` to ensure the printhead moves in the correct direction while homing.
[Klipper Configuration Reference](https://www.klipper3d.org/Config_Reference.html?h=pixel#stepper)

Looking forward to your insights. Thanks!

ambarusa, 2025-03-11:
Thanks for the feedback. This looks totally fine!

To use the VZPrinthead solution, why don't we add a simple box in one of the screwholes on the left side of the rail (exactly the way you did with your part), whose role is just to trigger the switch?

I will definitely try it after I have a working printer. :)

ambarusa, 2025-03-14:
Interestingly, my printer was equipped with the same piece of plastic under the endstop switches, so I just had to reinstall it with a longer M3 screw, and a washer, instead of the original M4 screw. So the conclusion is that it can be fixed without additional printing in advance.

Closed 2025-03-14.

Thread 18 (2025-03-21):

Ender 5 Pro uses M4 bolts and tnuts

wildstar87, 2025-03-21:
I'm a bit confused on one part of this.  In Stage 1, the instructions say to reuse the M3 bolts and tnuts, when assembling the Front Corner Assembly.  The screws I have in my Ender 5 Pro, are M4 bolts and tnuts.  They use an M3 allen wrench, and the thread diameter measures out at a little under 4mm.  Is this possibly a typo?  I'm wondering if the holes in the models are going to be big enough for me to use my existing M4 bolts/nuts or if I will have to buy M3 bolts and nuts to replace these, or just drill out the printed parts, and whether the screw holes have enough material for strength for me to do that?

Looking at a parts list for the Ender 5 Pro, it seems it definitely does use M4 bolts/tnuts.

https://www.3dmaterial.cz/files/shop/4-2022/creality/user-manual-ender-5-pro-en-v.2.1.pdf

wildstar87, 2025-03-25:
Probably want to update the docs, if/when the instructions are updated for v1.1.  I did check the models, and the holes definitely seem big enough for M4, so it definitely looks like a typo

DaKue77, 2025-03-25:
@wildstar87 I can also confirm M4 to be the original bolt size, at least on my Ender 5 Pro model.

endorphin3d, 2025-05-27:
Thanks for this. It's been fixed now.

Closed 2025-05-27.

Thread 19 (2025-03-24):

Driving X-mount difference between v1.1 and main?

wildstar87, 2025-03-24:
I started printing this mount out, and noticed that the v1.1 version has a notch in the top surface, vs a smooth top on the one in main.  What is the reasoning for the notch?  I would think this would add a potential weakness to the part.

endorphin3d, 2025-03-25:
That notch is for you to access the grub screw on the gear with a hex key for better alignment of the belt. Considering how much this mount was beefed up in other places for 1.1, I don't think this notch will be an issue.

wildstar87, 2025-03-25:
I see, I'm trying to swap over the extruder motor to X-axis, but the shaft is shorter, and round.  I was able to remove the gear, and bevel out a flat spot on the shaft, to use the existing timing gear, hopefully it won't need to be moved up much further, otherwise I may have to get another stepper with a longer shaft.

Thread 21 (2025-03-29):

Suggestion for Marlin FW / layer shifting

tocsa120ls, 2025-03-29:
The mod works perfect (Ender 5 Pro + v4.2.7 mainboard + Stage1 so far with me) but the firmware configuration can give headaches. Just want to drop a few tips, and the issues I've experienced:

* forget the mainline Marlin firmware. It is about 15 months behind the _bugfix-2.1.x_ branch and so many things were fixed, especially regarding CoreXY kinematics. Do not use the mainline.

* my alterations to the (bugfix) firmware:

* uncomment these 2 lines in _Configuration.h_
```
#define MARKFORGED_XY
#define MARKFORGED_INVERSE  // Enable for an inverted Markforged kinematics belt path
```

* if you have swapped the X stepper with the extruder stepper, you can and probably need to up the current of the motor since we removed the weight from the X gantry, but we added 4 pulleys to the belt path - for me this was causing the random layer shifting issues in one direction

* adjust these 2 values in _Configuration_adv.h_
```
    #define X_CURRENT       650        // (mA) RMS current. Multiply by 1.414 for peak current.
```
crank it up from 580 - I matched the Y_CURRENT which is 650

* similarly, the extruder stepper is small now
```
    #define E0_CURRENT      580
```
reduce the current to 580

That's it.

jjn-9306, 2025-05-02:
I will try this after the current print finished. I swapped the X and E motors but did not change anything else. I am noticing when the print head travels along the Y = -X line, the X motor makes a loud buzzing noise. I'm guessing this is because the combined X/Y motion in that direction is forcing the motor to move faster than it can safely keep up?

I'm hoping increasing the V_ref and changing the current will fix the issue.

endorphin3d, 2025-05-02:
Yeah so I'm pretty certain that sound comes from the slight positional inaccuracies that come from stealthchop. My theory is one stepper corrects the other and causes some jerking motion (leading to vibration = sound).

The reason for this theory is when I turn off stealthchop and increasing my microsteps to 128. Basically getting increased torque and positional accuracy while approaching the same level of quiet as stealthchop

Unfortunately the 4.2.7 board has stealthchop hard wired so you'll need to do some soldering or change boards.

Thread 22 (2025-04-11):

Requesting a version that uses 5mm bore pulleys

wildstar87, 2025-04-11:
The 3mm bore pulleys that seem to be available, I have found, don't have enough effective clearance between the bearing core on the outer, so even with washers on both sides, tightening these down, will cause binding, increasing friction dramatically.  There seems to be much fewer options, since this is a more uncommon bore size.  I know that the 3mm bore was decided on to reuse the stock carriage holes without modification in a Stage 1.

I went directly to Stage 2, and trying to keep the pulleys loose enough that they don't bind, while keeping them from wobbling is difficult, and can loosen up tolerances just by being used, I think because the wobble wears on the 3d printed parts, causing them to loosen up, even when using nylock nuts.

The more common 5mm pulleys have much more selection, and would probably be easier to ones with bearings that had proper clearance, that wouldn't bind when tightened down.

Would be nice to have a version that used 5mm bore pulleys in addition to the existing 3mm design.

Zoolander06, 2025-04-21:
Hello,

You could very easily design some spacers to put inside your 5mm bore pulleys.
I had old belt tensioner reusing the original pulleys with that kind of spacer to use M5 bolts instead of the genuine M8, and it worked perfectly.
The issue I have with 3mm bore pulleys is that washers are to big and prevent me to tighten screws correctly, perhaps thats what causing your issues. For that, perhaps some printed washers 5x0.6mm would help.

endorphin3d, 2025-04-22:
Yes I like @Zoolander06's idea of making an adapter that would slot into a 5mm bore. That's far more preferable to redesigning almost every part in the system plus modifying all the docs. If anyone wants to design that, you can make a PR and I'll review it. Please include a STEP file so I can integrate it into the project.

Elucubra, 2025-05-15:
Hola.
Is there a good reason why the holes can't be redrilled to 5mm? Trivial with a bench drill adapter or similar.

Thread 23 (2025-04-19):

Belts are interfering with frame

Zoolander06, 2025-04-19:
Hello,
I started to convert my Ender 5 Pro, but quickly ran into an issue : the 20 teeth pulleys on the Y belt tensioner are too small, and the belt is ripping against the frame extrusion.
The original pulleys on the Ender 5 Pro are 28 teeth.
What I don't understand is that I seem to be the only one who encountered this issue... Is there something I missed ?

Joris

Zoolander06, 2025-04-19:
Sorry, I thought the issue was related to the small diameter of the pulleys, but it was related to the washer that I put while mounting the pulley. I removed the washers and everything seems to work normally now.

Closed 2025-04-19.

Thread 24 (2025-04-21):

Unparallel belt travel

Zoolander06, 2025-04-21:
Hello, I noticed that the hybrid belt travel slightly not parallel to the Y axis. I think it would be better that everything is parallel, for better accuracy.
It would be solved by moving the stepper motor, and the idler 2mm to the left (with a 1.5mm thick belt).

Also, the travel along the X axis is only parallel with the genuine idler, with the shitty tensioning system. If you use the Endorphin tensioner, with the 20 teets pulley, the belt is not parallel anymore. I made some modifications on the tensioner mover so it can reuse the original 28 teeth idler, but I hadn't tested it yet...

Am I wrong ?

Joris

endorphin3d, 2025-05-04:
Would you mind posting a few photos? I can't quite visualize the issue you're seeing.

Zoolander06, 2025-05-16:
Hello,
Well, you can easily see the issue on the cad model :
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
Let's forget the belt, which is only there for looking good since it doesn't even touch any of the pulleys, and you can see that there's about 3.5mm between the idlers on the X gantry, and the driving pulley. Same with the idler of the corner assembly. So, the X belt is not running perfectly parallel to the Y axis, which, I believe, can lead to unequal tension depending of the Y position.
This part is easy to correct, you just need to move both the motor and the front corner idler so the belt run perfectly parallel (I would do it myself but since I don't have the design history in the step file, it's a real nightmare).

There's a similar problem along the X axis, which is already there on the original Ender 5. I think I could solve it by putting some spacers on the X carriage.

I don't know exactly how much it impacts the precision of the printer, but I think that, since it's a simple fix, it's always better...

I hope this is clear, english is not my main language, so it sometimes difficult for me to explain...

Joris

Elucubra, 2025-05-21:
Joris,
Calling the work of someone who has spent a lot of time and effort, and sharing it for free, shitty is disrespectful at best, I would call it disgraceful.

Please indicate where is this lack of parallel

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

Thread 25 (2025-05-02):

Endorphin logo image

ambarusa, 2025-05-02:
Hi,

Could you please share the Endorphin logo with us? I want to make a nice bed texture in my slicer to replace the boring grid.

Thanks,
Adam

endorphin3d, 2025-05-04:
There's two in the repo currently:

- https://github.com/endorphin3d/endorphin/blob/main/assets/images/icon.svg
- https://github.com/endorphin3d/endorphin/blob/main/assets/images/logo.svg

Does that work or do you need another format?

ambarusa, 2025-05-05:
Ah, so sorry! Totally overlooked the `assets` folder.

Closed 2025-05-05.

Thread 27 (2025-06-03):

Recomended material for parts

C0untZero, 2025-06-03:
Hey! First off, thanks for sharing this awesome project with the community, been eyeing it for a while now.

One question - what is the recommended material for printing all those parts? Is regular PLA ok? Or do we need something more sturdy?

Perhaps the answer to this could also be added to the instructions ;)

Thanks in advance!

CantElevate, 2025-06-13:
I printed mine in ABS with the Voron specification, 5 top/bottom 4 perimeters and 40% infill   I figure if it works for the mercury one.1 and other printers, it should work well here too.  I would say your choice would depend on what and how you choose to print, heated enclosure, probably wants abs, as PLA and PETG become putty when hot.

Closed 2025-08-10.

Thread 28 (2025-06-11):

Debris from the belts around the tensioners

ambarusa, 2025-06-11:
Hello,

After a while of using the X tensioner, I noticed some debris from the belts due to the touching the sharp edges of the rails. I can definitely imagine that this affects the print quality as the belts are not completely moving free.

I can also notice that even the belts on the Y axis are touching the edges of the rails.

Does this occur to you?

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

ambarusa, 2025-06-11:
I would also be interested if you think necessary to add washers to the X tensioner. Even though the pulley is in horizontal position, I can see that it never lifts up or down to touch the plastic. For the Y ones, the guide clearly mentions that washers are not so important. It is really hard to push them on both sides of the pulley anyway.

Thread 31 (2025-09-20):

Stage 2 instructions are confusing

kozross, 2025-09-20:
According to the written instructions, the CAD model and the images, the right Y rail is mounted on the ouside of the frame. However, the video (at least to me) appears to mount it on the _in_side. This is quite confusing and should probably be fixed: I suspect a lot of people would watch the video before reading.

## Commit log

2023-04-30 Commit progress on stage 1
2023-05-14 Add belt path render
2023-05-14 More assembly vids
2023-05-14 Add stage 1 BOM
2023-05-17 Finish stage 1 docs
2023-05-19 Work on stage 2
2023-05-20 Begin stage 3
2023-05-20 Add EVA docs
    [back_endorphin.stl, endorphin_belt_grabber.stl]
2023-06-12 More docs
    [eva-mgn9h.stl]
2023-06-13 Add Vz docs
    [belt_clip-touthed.stl, eva-back_endorphin.stl, vz-back_plate.stl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]
2023-06-27 Add right linear Y rail docs
2023-06-27 Move STLs
    [belt_clip-touthed.stl, eva-back_endorphin.stl, eva-mgn9h.stl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]
2023-06-27 Add CAD files
    [center-idler-bottom.stl, center-idler-top.stl, driving-x-mount.stl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]
2023-08-12 Add STL link in step docs
2023-08-13 Clarify stage 3 weight add
2023-08-22 Recommend 350mm for X rail
2023-09-30 Add Klipper settings for proper homing
2023-10-13 EVA belt grabber was misnamed
    [eva-endorphin_belt_grabber.stl]
2025-01-11 Add 2nd Y tensioner, EVA printhead
2025-01-11 Add Y tensioner STL
    [y-tensioner-housing.stl]
2025-01-30 Add right-linear-y-top.stl
    [right-linear-y-top.stl]
2025-02-10 Add X axis tensioner
    [x-tensioner-housing.stl]
2025-03-06 Add stage 2 linear rails
    [left-linear-y.stl, right-linear-y.stl]
2025-03-12 Add cable guide STL
    [cable-guide.stl]
2025-03-12 Add v1.1 stage 1 files
    [center-idler-top.stl, driving-x-mount.stl, front-corner-assembly.stl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]
2025-03-12 Update tensioner
    [y-tensioner-housing.stl]
2025-03-12 Update X tensioner
2025-05-27 Finish 1.1 docs
    [tensioner-knob.stl, tensioner-slider.stl, y-tensioner-housing.stl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]
2025-05-27 M4 T-nut typo
2025-06-11 Add stage 3 STL link
